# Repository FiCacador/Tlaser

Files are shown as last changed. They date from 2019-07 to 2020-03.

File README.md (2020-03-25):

# Tlaser

Tlaser is a laser engraver designed as proof of concept of a new motion system, coreXY cantilever. It's called Tlaser because this motion system, and thus this machine, is shaped like a T.  
  
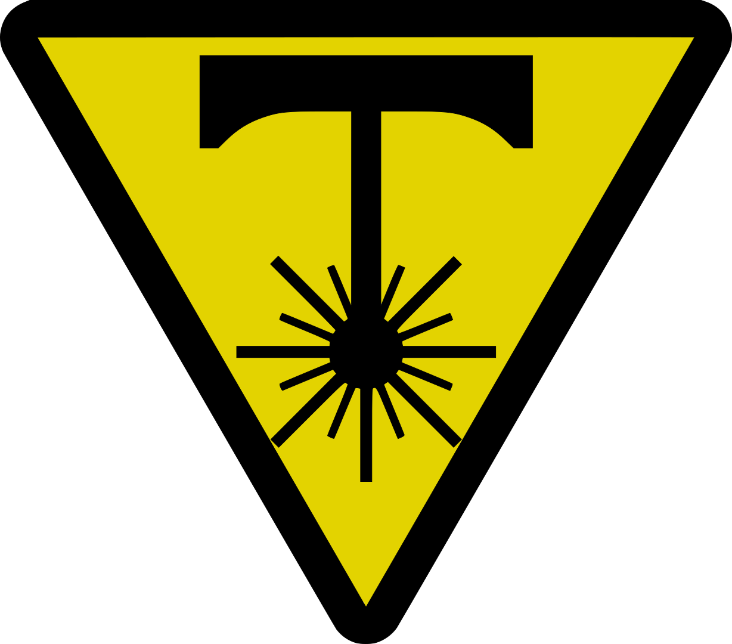
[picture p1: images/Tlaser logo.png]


### Main features:

- **CoreXY cantilever**
- **5500mW blue laser**
- **315mm x 205mm engraving area**
- **Linear guide rails**
- **Adjustable height at each corner**
- **3D printed**  
  
## [Video of Tlaser in action!](https://youtu.be/NjZCqPt6v3c)

<p float="center">
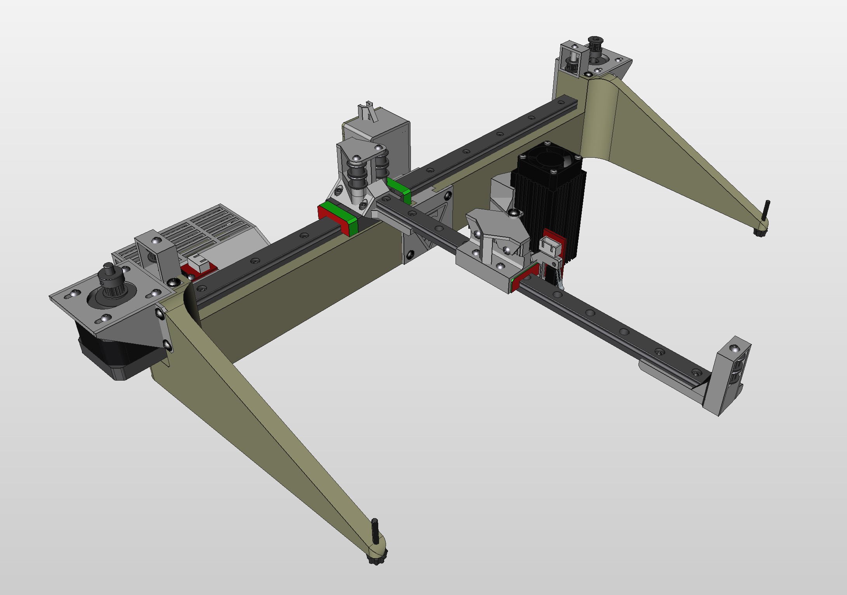
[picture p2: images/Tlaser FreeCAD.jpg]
  
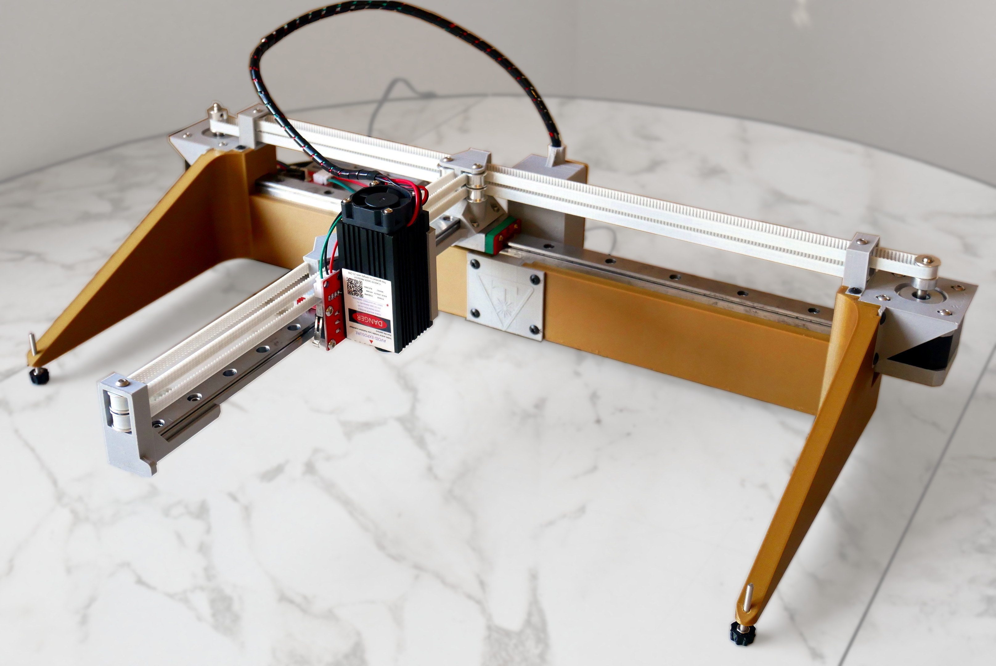
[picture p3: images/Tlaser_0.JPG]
  
</p>

## CoreXY cantilever

Tlaser was developed to validate and demonstrate a new motion system, which the author named  *CoreXY cantilever*.  
CoreXY cantilever has the same kinematics as [CoreXY](https://corexy.com/theory.html), so it is easy to configure in existing firmware like Grbl or Marlin. If the motors rotate to the same directions, the head travels along the X axis. If the motors rotate to opposite directions, the head travels along the Y axis.  
This mechanism has two belts, one over another, each on a circuit shaped like a T. Both circuits have pulleys at the middle on both sides and at the end of the cantilever.  
The upper belt is driven by the motor at the right end, has a pulley on the left end and is locked to the left side of the carrier. The lower is symmetric, motor on the left, pulley on the right, locked to the right side of the carrier.

<p float="center">
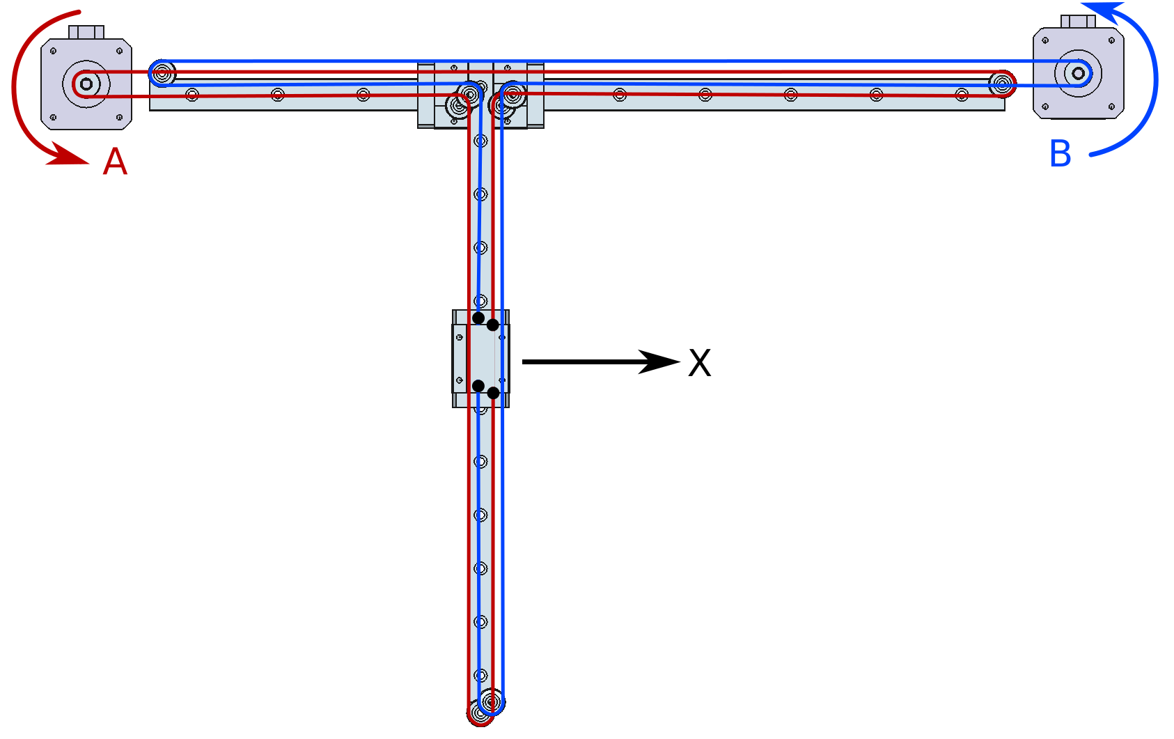
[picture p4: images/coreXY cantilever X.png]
  
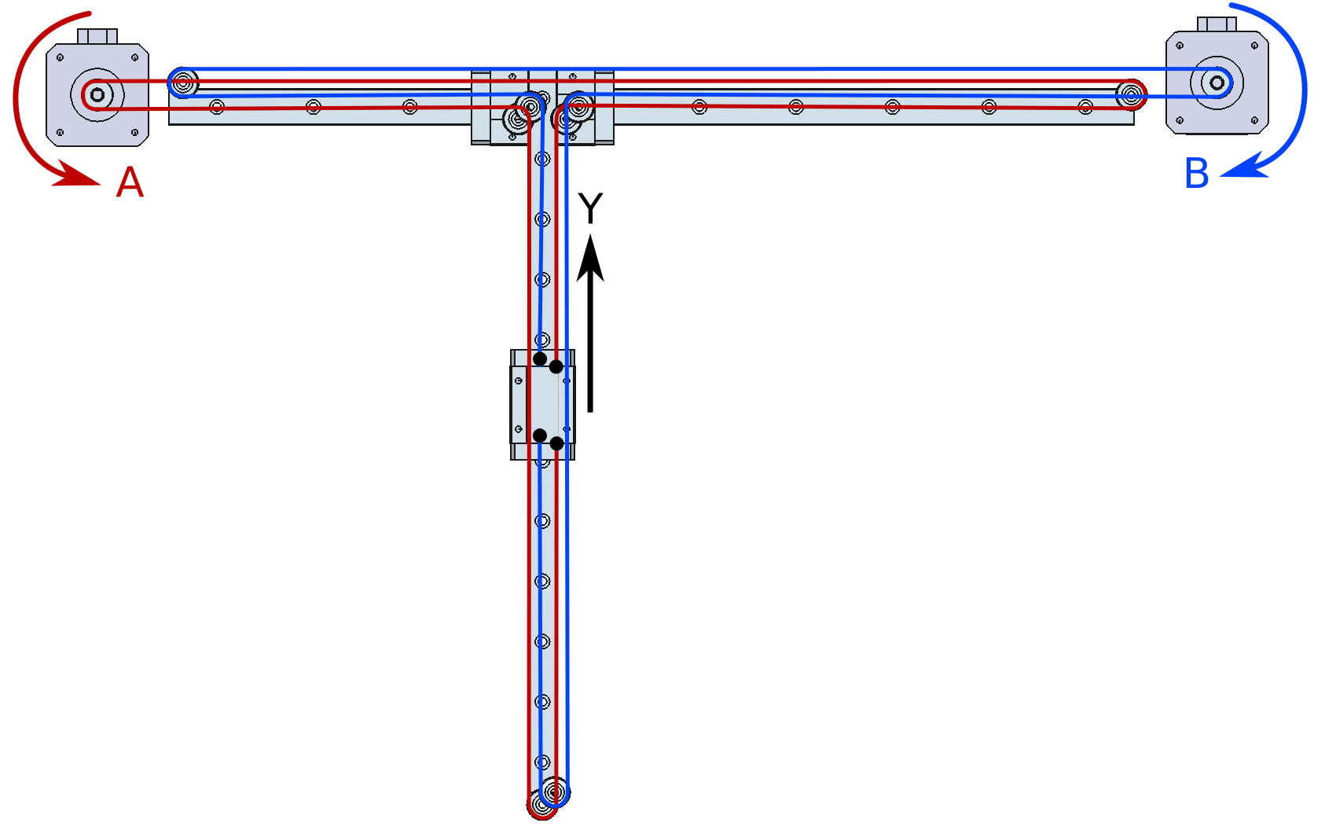
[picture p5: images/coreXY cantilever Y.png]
  
</p>

## Hardware

The following parts are required for building this machine:

- [5.5W 445NM blue laser module w/ power supply](http://s.click.aliexpress.com/e/bAbwR1Wg)
- [MGN12H 300mm and MGN15H 400mm Blocks and Rails](http://s.click.aliexpress.com/e/bKj8dYfI)
- [2 Nema 17 stepper motors](http://s.click.aliexpress.com/e/cpg92iXI)
- [Arduino Uno R3 /w CNC shield v3 and A4988 stepper drivers](http://s.click.aliexpress.com/e/b7E6Xk5a)
- [2 mechanical endstops](http://s.click.aliexpress.com/e/CIG3mQk)
- [Timing belt GT2 6mm 5m](http://s.click.aliexpress.com/e/belvtmGu)
- [2 Belt drive Pulleys GT2 16 teeth bore 5mm](https://s.click.aliexpress.com/e/_d7v8uTQ)
- [GT2 pulleys, 4 w/ 16 teeth and 4 w/ no teeth](https://s.click.aliexpress.com/e/_dZuRE9S)
- [M3x6 and M3x30 round head hex bolts](http://s.click.aliexpress.com/e/cScWFTX6)
- [M3x8 socket head hex bolts](http://s.click.aliexpress.com/e/b72TH5Nm)
- [M3x12 self tapping bolts](http://s.click.aliexpress.com/e/bZMmlnQu)
- [M3x50 socket head bolts](http://s.click.aliexpress.com/e/t3QLC2k)
- [M3 hex nuts](http://s.click.aliexpress.com/e/nRG0NIC)

The list above contains affiliate links.  
The total cost should be below €150 / $165 USD, 3D printed parts not included.
For a more detailed table with quantities check the [Bill of Materials](https://github.com/FiCacador/Tlaser/raw/master/BOM.ods).

## 3D Printed parts

All parts are already correctly oriented for ease of printing and available in [STL files](https://github.com/FiCacador/Tlaser/tree/master/STLs) and [AMF files](https://github.com/FiCacador/Tlaser/tree/master/AMFs).  
Dimensional accuracy is very important. This is an assembly of mechanical parts designed to fit tight, the slightest overextrusion will make for a hard time during the assembly.  
Due to proximity to the stepper motors and laser module, [Laser Mount](https://github.com/FiCacador/Tlaser/blob/master/STLs/Laser%20Mount.stl), [Motor Mount Left](https://github.com/FiCacador/Tlaser/blob/master/STLs/Motor%20Mount%20Left.stl) and [Motor Mount Right](https://github.com/FiCacador/Tlaser/blob/master/STLs/Motor%20Mount%20Right.stl) should be printed with a more heat resistant material, like ABS or PETG.  
Recommended settings: 0.5 mm line width, 0.2 mm layer height, 2 mm wall thickness, over 15% infill. Some parts require support. [Base Left](https://github.com/FiCacador/Tlaser/blob/master/STLs/Base%20Left.stl) and [Base Right](https://github.com/FiCacador/Tlaser/blob/master/STLs/Base%20Right.stl) are prone to warping, requiring good bed adhesion.  
Total printing time around 38h. Total filament used approximately 600g.

## Assembly

### [Video of Tlaser Exploded Assembly on FreeCAD](https://youtu.be/6Z7JV-q1IXA)

An [Exploded Assembly CAD file](https://github.com/FiCacador/Tlaser/raw/master/CAD/Tlaser%20Exploded%20Assembly.FCStd) for [FreeCAD](https://www.freecadweb.org/) with the [Exploded Assembly workbench](https://github.com/JMG1/ExplodedAssembly) added is available to guide the assembly process.  
Required tools are a set of hex key wrenches, a philips screwdriver, a small flat head screwdriver, a rubber mallet and a wire cutter.  
The controller wiring is pretty straight forward, the exceptions being the laser TTL connects to the Z+ endstop pins and the red wire is left out when connecting the X and Y endstops. The power supply and 12V laser PCB cables need to be cut so both can be connected to the same respective + and - on the CNC shield.

<p float="center">
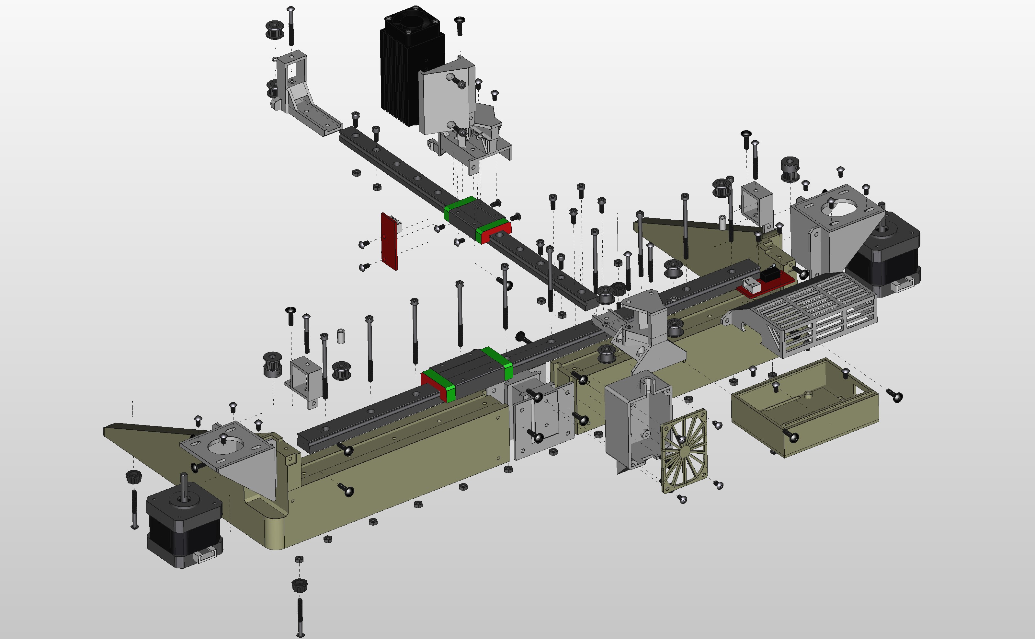
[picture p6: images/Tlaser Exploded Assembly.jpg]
  
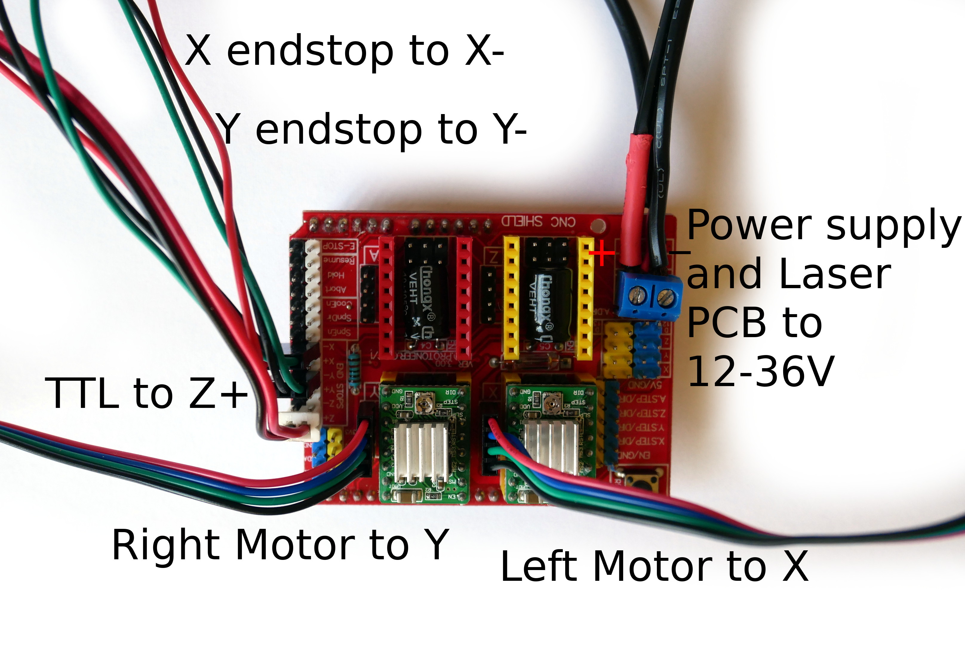
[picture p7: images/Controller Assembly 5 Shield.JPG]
  
</p>

## Firmware

An Arduino running [Grbl](https://github.com/gnea/grbl) is used to control Tlaser. It uses Grbl version 1.1g with a modified [config.h file](https://github.com/FiCacador/Tlaser/blob/master/Firmware/grbl-v1.1/grbl/config.h) with the configuration and default values that better suit this machine.  
You can find an hex file and the source code of Grbl for Tlaser [here](https://github.com/FiCacador/Tlaser/tree/master/Firmware).  
Instructions on how to [flash Grbl to an Arduino](https://github.com/gnea/grbl/wiki/Flashing-Grbl-to-an-Arduino) or alternatively [compile and upload Grbl](https://github.com/gnea/grbl/wiki/Compiling-Grbl) can be found on the [Grbl Wiki](https://github.com/gnea/grbl/wiki).  
Grbl is distributed under the GPLv3 license and is developed by Sungeun K. Jeon Ph.D.

## CAM Software

[LaserWeb4](https://github.com/LaserWeb/LaserWeb4/wiki) is simple yet powerful, graphically pleasing open source laser CAM software available for Windows, Mac and Linux.  
A [file containing Tlaser profile](https://github.com/FiCacador/Tlaser/blob/master/CAM%20profiles/laserweb-profiles-tlaser.json) for LaserWeb4 v4.0.996 is available.  
There are many valid laser CAM software options, use whatever one you like the most.

## Design

This project was designed using [FreeCAD](https://www.freecadweb.org/). There are more powerful and certainly more user friendly options, but none is actually free (of charge, of licensing, of login) and available for Windows, Mac and Linux.  
Designed with FreeCAD version 0.18.3 with the added workbenches [Fasteners](https://github.com/shaise/FreeCAD_FastenersWB), [A2plus](https://github.com/kbwbe/A2plus) and [Exploded Assembly](https://github.com/JMG1/ExplodedAssembly).  
You can find the CAD files for the individual parts and the assembly [here](https://github.com/FiCacador/Tlaser/tree/master/CAD).  
All the features and sketches of the 3D Printed parts are named, for ease of understanding and editing

---

Tlaser is developed by Filipe Caçador.

## License

Tlaser is published under the Creative Commons [Attribution-ShareAlike 4.0 International (CC BY-SA 4.0)](https://creativecommons.org/licenses/by-sa/4.0/) Public License.  
Under this license, anyone can share, copy, redistribute, edit, remix and develop this work, for any purpose, as long as credit is attributed to the original author and any further developments are distributed under the same license.  
No warranty of any kind is provided and the author is not liable for any losses, damages or injuries in any way related to this work.

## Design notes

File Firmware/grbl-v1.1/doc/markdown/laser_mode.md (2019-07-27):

## Grbl v1.1 Laser Mode

**_DISCLAIMER: Lasers are extremely dangerous devices. They can instantly cause fires and permanently damage your vision. Please read and understand all related documentation for your laser prior to using it. The Grbl project is not resposible for any damage or issues the firmware may cause, as defined by its GPL license._**

----

Outlined in this document is how Grbl alters its running conditions for the new laser mode to provide both improved performance and attempting to enforce some basic user safety precautions.

## Laser Mode Overview

The main difference between default Grbl operation and the laser mode is how the spindle/laser output is controlled with motions involved. Every time a spindle state `M3 M4 M5` or spindle speed `Sxxx` is altered, Grbl would come to a stop, allow the spindle to change, and then continue. This is the normal operating procedure for a milling machine spindle. It needs time to change speeds. 

However, if a laser starts and stops like this for every spindle change, this leads to scorching and uneven cutting/engraving! Grbl's new laser mode prevents unnecessary stops whenever possible and adds a new dynamic laser power mode that automagically scales power based on current speed related to programmed rate. So, you can get super clean and crisp results, even on a low-acceleration machine!

Enabling or disabling Grbl's laser mode is easy. Just alter the **$32** Grbl setting. 
- **To Enable**: Send Grbl a `$32=1` command. 
- **To Disable:** Send Grbl a `$32=0` command.

**WARNING:** If you switch back from laser mode to a spindle for milling, you **MUST** disable laser mode by sending Grbl a `$32=0` command. Milling operations require the spindle to get up to the right rpm to cut correctly and to be **safe**, helping to prevent a tool from breaking and flinging metal shards everywhere. With laser mode disabled, Grbl will briefly pause upon any spindle speed or state change to give the spindle a chance to get up to speed before continuing.

## Laser Mode Operation

When laser mode is enabled, Grbl controls laser power by varying the **0-5V** voltage from the spindle PWM D11 pin. **0V** should be treated as disabled, while **5V** is full power. Intermediate output voltages are also assumed to be linear with laser power, such that **2.5V** is approximate 50% laser power. (A compile time option exists to shift this linear model to start at a non-zero voltage.) 

By default, the spindle PWM frequency is **1kHz**, which is the recommended PWM frequency for most current Grbl-compatible lasers system. If a different frequency is required, this may be altered by editing the `cpu_map.h` file. 

The laser is enabled with the `M3` spindle CW and `M4` spindle CCW commands. These enable two different laser modes that are advantageous for different reasons each.
	
- **`M3` Constant Laser Power Mode:**

    - Constant laser power mode simply keeps the laser power as programmed, regardless if the machine is moving, accelerating, or stopped. This provides better control of the laser state. With a good G-code program, this can lead to more consistent cuts in more difficult materials. 
    
    - For a clean cut and prevent scorching with `M3` constant power mode, it's a good idea to add lead-in and lead-out motions around the line you want to cut to give some space for the machine to accelerate and decelerate.

    - NOTE: `M3` can be used to keep the laser on for focusing.

- **`M4` Dynamic Laser Power Mode:**
    - Dynamic laser power mode will automatically adjust laser power based on the current speed relative to the programmed rate. It essentially ensures the amount of laser energy along a cut is consistent even though the machine may be stopped or actively accelerating. This is very useful for clean, precise engraving and cutting on simple materials across a large range of G-code generation methods by CAM programs. It will generally run faster and may be all you need to use.
    
    - Grbl calculates laser power based on the assumption that laser power is linear with speed and the material. Often, this is not the case. Lasers can cut differently at varying power levels and some materials may not cut well at a particular speed and/power. In short, this means that dynamic power mode may not work for all situations. Always do a test piece prior to using this with a new material or machine.
		
    - When not in motion, `M4` dynamic mode turns off the laser. It only turns on when the machine moves. This generally makes the laser safer to operate, because, unlike `M3`, it will never burn a hole through your table, if you stop and forget to turn `M3` off in time.

Describe below are the operational changes to Grbl when laser mode is enabled. Please read these carefully and understand them fully, because nothing is worse than a garage _**fire**_.

- Grbl will move continuously through **consecutive** motion commands when programmed with a new `S` spindle speed (laser power). The spindle PWM pin will be updated instantaneously through each motion without stopping.
	- Example: The following set of g-code commands will not pause between each of them when laser mode is enabled, but will pause when disabled.
	
		```
		G1 X10 S100 F50
		G1 X0 S90
		G2 X0 I5 S80
		``` 
	- Grbl will enforce a laser mode motion stop in a few circumstances. Primarily to ensure alterations stay in sync with the g-code program.

		- Any `M3`, `M4`, `M5` spindle state _change_. 
		- `M3` only and no motion programmed: A `S` spindle speed _change_.
		- `M3` only and no motion programmed: A `G1 G2 G3` laser powered state _change_ to `G0 G80` laser disabled state.
		- NOTE: `M4` does not stop for anything but a spindle state _change_.

- The laser will only turn on when Grbl is in a `G1`, `G2`, or `G3` motion mode. 

	- In other words, a `G0` rapid motion mode or `G38.x` probe cycle will never turn on and always disable the laser, but will still update the running modal state. When changed to a `G1 G2 G3` modal state, Grbl will immediately enable the laser based on the current running state.
	
	- Please remember that `G0` is the default motion mode upon power up and reset. You will need to alter it to `G1`, `G2`, or `G3` if you want to manually turn on your laser. This is strictly a safety measure.
	
	- Example: `G0 M3 S1000` will not turn on the laser, but will set the laser modal state to `M3` enabled and power of `S1000`. A following `G1` command will then immediately be set to `M3` and `S1000`.

	- To have the laser powered during a jog motion, first enable a valid motion mode and spindle state. The following jog motions will inherit and maintain the previous laser state. Please use with caution though. This ability is primarily to allow turning on the laser on a _very low_ power to use the laser dot to jog and visibly locate the start position of a job.

- An `S0` spindle speed of zero will turn off the laser. When programmed with a valid laser motion, Grbl will disable the laser instantaneously without stopping for the duration of that motion and future motions until set greater than zero..

	- `M3` constant laser mode, this is a great way to turn off the laser power while continuously moving between a `G1` laser motion and a `G0` rapid motion without having to stop. Program a short `G1 S0` motion right before the `G0` motion and a `G1 Sxxx` motion is commanded right after to go back to cutting.

-----
###CAM Developer Implementation Notes

TODO: Add some suggestions on how to write laser G-code for Grbl. 

- When using `M3` constant laser power mode, try to avoid force-sync conditions during a job whenever possible. Basically every spindle speed change must be accompanied by a valid motion. Any motion is fine, since Grbl will automatically enable and disable the laser based on the modal state. Avoid a `G0` and `G1` command with no axis words in this mode and in the middle of a job.

- Ensure smooth motions throughout by turning the laser on and off without an `M3 M4 M5` spindle state command. There are two ways to do this:

    - _Program a zero spindle speed `S0`_: `S0` is valid G-code and turns off the spindle/laser without changing the spindle state. In laser mode, Grbl will smoothly move through consecutive motions and turn off the spindle. Conversely, you can turn on the laser with a spindle speed `S` greater than zero. Remember that `M3` constant power mode requires any spindle speed `S` change to be programmed with a motion to allow continuous motion, while `M4` dynamic power mode does not.

    - _Program an unpowered motion between powered motions_: If you are traversing between parts of a raster job that don't need to have the laser powered, program a `G0` rapid between them. `G0` enforces the laser to be disabled automatically. The last spindle speed programmed doesn't change, so if a valid powered motion, like a `G1` is executed after, it'll immediately re-power the laser with the last programmed spindle speed when executing that motion.

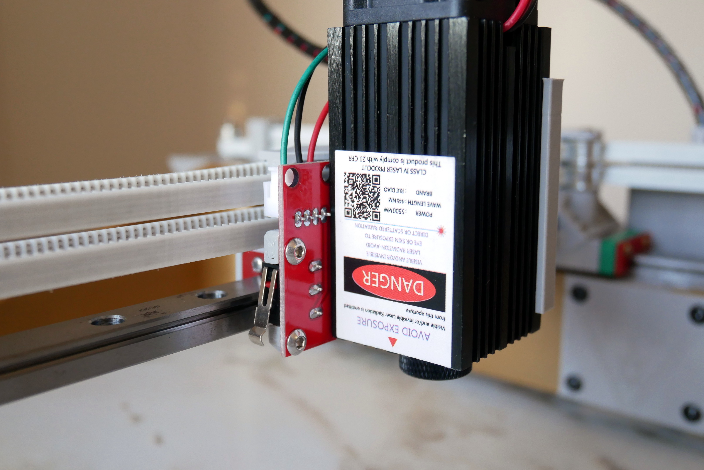
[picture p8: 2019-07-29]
images/Tlaser_8.JPG

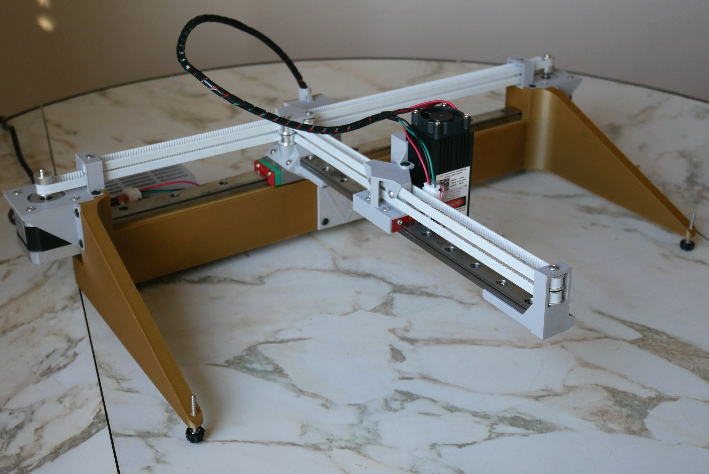
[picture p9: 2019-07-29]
images/Tlaser_1.JPG

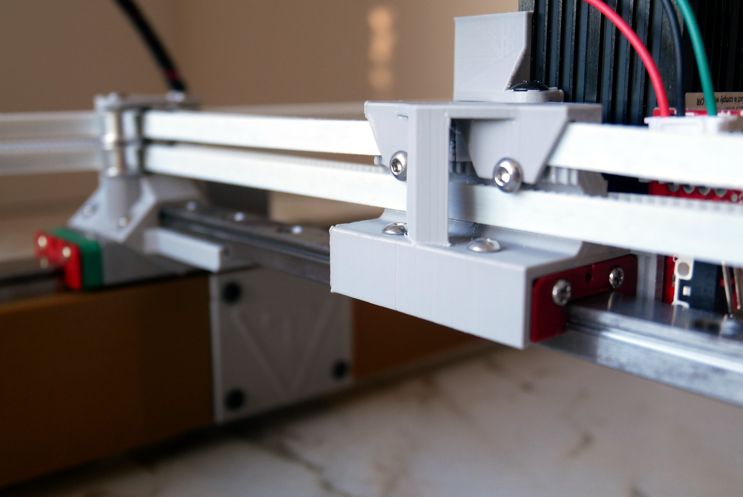
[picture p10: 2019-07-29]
images/Tlaser_5.JPG

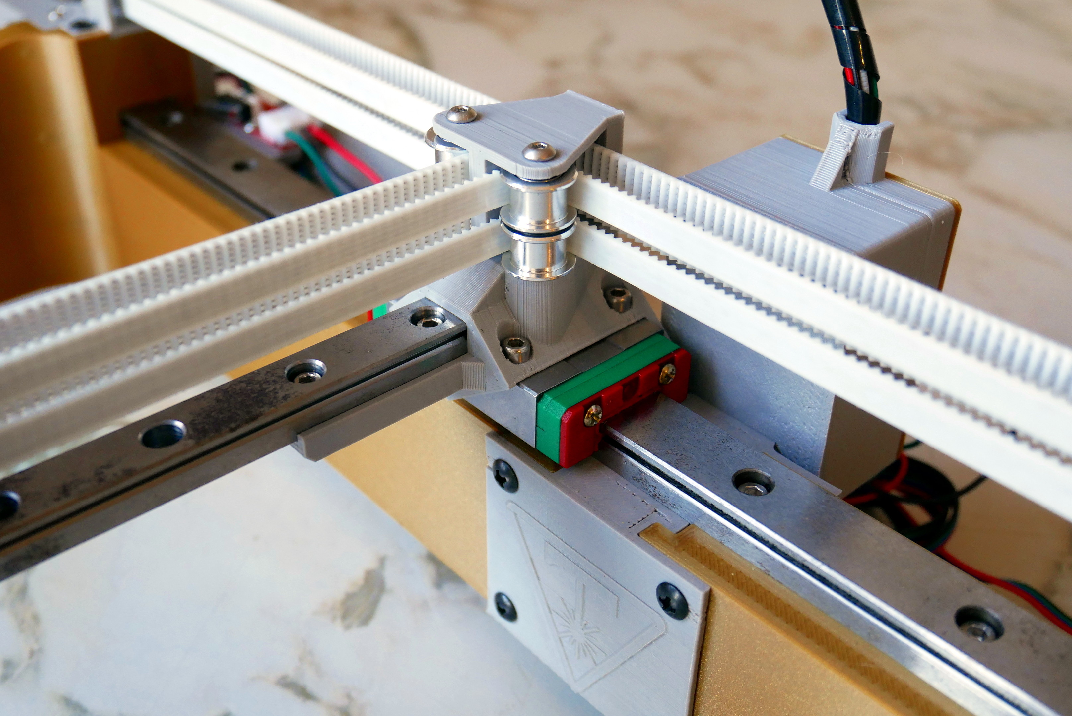
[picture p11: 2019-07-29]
images/Tlaser_6.JPG

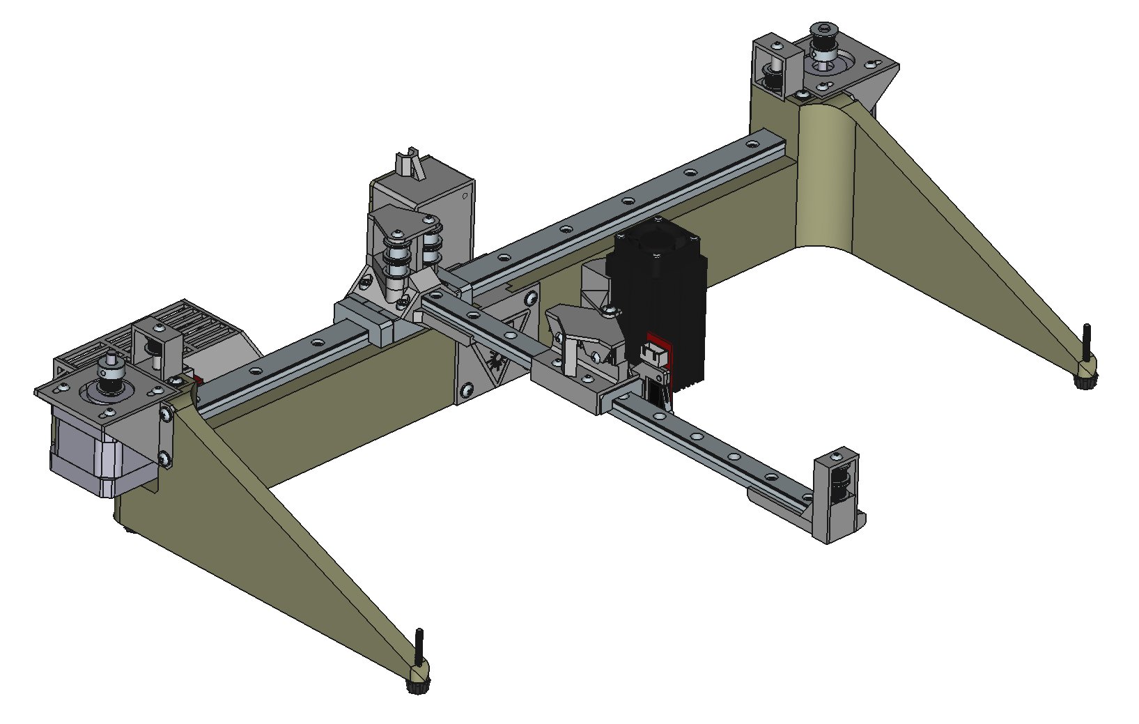
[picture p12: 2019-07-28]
images/Tlaser_FreeCAD.png

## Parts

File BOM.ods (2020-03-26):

Bill of Materials – Tlaser
3D Printed
Quantity | Description | STL file | CAD file | AMF file
1 | Base Left | stl (https://github.com/FiCacador/Tlaser/blob/master/STLs/Base%20Left.stl) | fcstd (https://github.com/FiCacador/Tlaser/raw/master/CAD/3D%20Printed/Base%20Left.FCStd) | amf (https://github.com/FiCacador/Tlaser/raw/master/AMFs/Base%20Left.amf)
1 | Base Middle | stl (https://github.com/FiCacador/Tlaser/blob/master/STLs/Base%20Middle.stl) | fcstd (https://github.com/FiCacador/Tlaser/raw/master/CAD/3D%20Printed/Base%20Middle.FCStd) | amf (https://github.com/FiCacador/Tlaser/raw/master/AMFs/Base%20Middle.amf)
1 | Base Right | stl (https://github.com/FiCacador/Tlaser/blob/master/STLs/Base%20Right.stl) | fcstd (https://github.com/FiCacador/Tlaser/raw/master/CAD/3D%20Printed/Base%20Right.FCStd) | amf (https://github.com/FiCacador/Tlaser/raw/master/AMFs/Base%20Right.amf)
4 | Bottom Stand | stl (https://github.com/FiCacador/Tlaser/blob/master/STLs/Bottom%20Stand.stl) | fcstd (https://github.com/FiCacador/Tlaser/raw/master/CAD/3D%20Printed/Bottom%20Stand.FCStd) | amf (https://github.com/FiCacador/Tlaser/raw/master/AMFs/Bottom%20Stand.amf)
1 | Controller Case Bottom | stl (https://github.com/FiCacador/Tlaser/blob/master/STLs/Controller%20Case%20Bottom.stl) | fcstd (https://github.com/FiCacador/Tlaser/raw/master/CAD/3D%20Printed/Controller%20Case%20Bottom.FCStd) | amf (https://github.com/FiCacador/Tlaser/raw/master/AMFs/Controller%20Case%20Bottom.amf)
1 | Controller Case Top | stl (https://github.com/FiCacador/Tlaser/blob/master/STLs/Controller%20Case%20Top.stl) | fcstd (https://github.com/FiCacador/Tlaser/raw/master/CAD/3D%20Printed/Controller%20Case%20Top.FCStd) | amf (https://github.com/FiCacador/Tlaser/raw/master/AMFs/Controller%20Case%20Top.amf)
1 | Endstop Mount | stl (https://github.com/FiCacador/Tlaser/blob/master/STLs/Laser%20Mount.stl) | fcstd (https://github.com/FiCacador/Tlaser/raw/master/CAD/3D%20Printed/Endstop%20Mount.FCStd) | amf (https://github.com/FiCacador/Tlaser/raw/master/AMFs/Laser%20Mount.amf)
1 | Laser Mount | stl (https://github.com/FiCacador/Tlaser/blob/master/STLs/Laser%20Mount.stl) | fcstd (https://github.com/FiCacador/Tlaser/raw/master/CAD/3D%20Printed/Laser%20Mount.FCStd) | amf (https://github.com/FiCacador/Tlaser/raw/master/AMFs/Laser%20Mount.amf)
1 | Laser PCB Box | stl (https://github.com/FiCacador/Tlaser/blob/master/STLs/Laser%20PCB%20Box.stl) | fcstd (https://github.com/FiCacador/Tlaser/raw/master/CAD/3D%20Printed/Laser%20PCB%20Box.FCStd) | amf (https://github.com/FiCacador/Tlaser/raw/master/AMFs/Laser%20PCB%20Box.amf)
1 | Laser PCB Box Lid | stl (https://github.com/FiCacador/Tlaser/blob/master/STLs/Laser%20PCB%20Box%20Lid.stl) | fcstd (https://github.com/FiCacador/Tlaser/raw/master/CAD/3D%20Printed/Laser%20PCB%20Box%20Lid.FCStd) | amf (https://github.com/FiCacador/Tlaser/raw/master/AMFs/Laser%20PCB%20Box%20Lid.amf)
1 | Motor Mount Left | stl (https://github.com/FiCacador/Tlaser/blob/master/STLs/Motor%20Mount%20Left.stl) | fcstd (https://github.com/FiCacador/Tlaser/raw/master/CAD/3D%20Printed/Motor%20Mount%20Left.FCStd) | amf (https://github.com/FiCacador/Tlaser/raw/master/AMFs/Motor%20Mount%20Left.amf)
1 | Motor Mount Right | stl (https://github.com/FiCacador/Tlaser/blob/master/STLs/Motor%20Mount%20Right.stl) | fcstd (https://github.com/FiCacador/Tlaser/raw/master/CAD/3D%20Printed/Motor%20Mount%20Right.FCStd) | amf (https://github.com/FiCacador/Tlaser/raw/master/AMFs/Motor%20Mount%20Right.amf)
1 | Pulley Cage Left | stl (https://github.com/FiCacador/Tlaser/blob/master/STLs/Pulley%20Cage%20Left.stl) | fcstd (https://github.com/FiCacador/Tlaser/raw/master/CAD/3D%20Printed/Pulley%20Cage%20Left.FCStd) | amf (https://github.com/FiCacador/Tlaser/raw/master/AMFs/Pulley%20Cage%20Left.amf)
1 | Pulley Cage Right | stl (https://github.com/FiCacador/Tlaser/blob/master/STLs/Motor%20Mount%20Right.stl) | fcstd (https://github.com/FiCacador/Tlaser/raw/master/CAD/3D%20Printed/Pulley%20Cage%20Right.FCStd) | amf (https://github.com/FiCacador/Tlaser/raw/master/AMFs/Motor%20Mount%20Right.amf)
1 | Rail Base | stl (https://github.com/FiCacador/Tlaser/blob/master/STLs/Rail%20Base.stl) | fcstd (https://github.com/FiCacador/Tlaser/raw/master/CAD/3D%20Printed/Rail%20Base.FCStd) | amf (https://github.com/FiCacador/Tlaser/raw/master/AMFs/Rail%20Base.amf)
1 | Rail Carrier | stl (https://github.com/FiCacador/Tlaser/blob/master/STLs/Rail%20Carrier.stl) | fcstd (https://github.com/FiCacador/Tlaser/raw/master/CAD/3D%20Printed/Rail%20Carrier.FCStd) | amf (https://github.com/FiCacador/Tlaser/raw/master/AMFs/Rail%20Carrier.amf)
1 | Rail Tip | stl (https://github.com/FiCacador/Tlaser/blob/master/STLs/Rail%20Tip.stl) | fcstd (https://github.com/FiCacador/Tlaser/raw/master/CAD/3D%20Printed/Rail%20Tip.FCStd) | amf (https://github.com/FiCacador/Tlaser/raw/master/AMFs/Rail%20Tip.amf)
3 | Spacer | stl (https://github.com/FiCacador/Tlaser/blob/master/STLs/Spacer.stl) | fcstd (https://github.com/FiCacador/Tlaser/raw/master/CAD/3D%20Printed/Spacer.FCStd) | amf (https://github.com/FiCacador/Tlaser/raw/master/AMFs/Spacer.amf)
2 | Tall Spacer | stl (https://github.com/FiCacador/Tlaser/blob/master/STLs/Tall%20Spacer.stl) | fcstd (https://github.com/FiCacador/Tlaser/raw/master/CAD/3D%20Printed/Tall%20Spacer.FCStd) | amf (https://github.com/FiCacador/Tlaser/raw/master/AMFs/Tall%20Spacer.amf)
Mechanical
Quantity | Description | Affiliate link | CAD file
1 | Rail MGN12 300mm | AliExpress (http://s.click.aliexpress.com/e/bKj8dYfI) | fcstd (https://github.com/FiCacador/Tlaser/raw/master/CAD/Mechanical/Rail%20MGN12%20300mm.fcstd)
1 | Block MGN12H | AliExpress (http://s.click.aliexpress.com/e/bKj8dYfI) | fcstd (https://github.com/FiCacador/Tlaser/raw/master/CAD/Mechanical/Block%20MGN12H.fcstd)
1 | Rail MGN15 400mm | AliExpress (http://s.click.aliexpress.com/e/bKj8dYfI) | fcstd (https://github.com/FiCacador/Tlaser/raw/master/CAD/Mechanical/Rail%20MGN15%20400mm.fcstd)
1 | Block MGN15H | AliExpress (http://s.click.aliexpress.com/e/bKj8dYfI) | fcstd (https://github.com/FiCacador/Tlaser/raw/master/CAD/Mechanical/Block%20MGN15H.fcstd)
1 | Timing Belt GT2 6mm 5m | AliExpress (http://s.click.aliexpress.com/e/belvtmGu)
2 | Belt Drive Pulley GT2 16 teeth 5mm | AliExpress (https://s.click.aliexpress.com/e/_d7v8uTQ) | fcstd (https://github.com/FiCacador/Tlaser/raw/master/CAD/Mechanical/Driver%20Pulley.fcstd)
4 | Pulley GT2 6mm 16T no teeth Bore 3mm | AliExpress (https://s.click.aliexpress.com/e/_dZuRE9S) | fcstd (https://github.com/FiCacador/Tlaser/raw/master/CAD/Mechanical/Pulley.fcstd)
4 | Pulley GT2 6mm 16T with teeth Bore 3mm | AliExpress (https://s.click.aliexpress.com/e/_dZuRE9S) | fcstd (https://github.com/FiCacador/Tlaser/raw/master/CAD/Mechanical/Pulley%2016T.FCStd)
Fasteners
Quantity | Description | Affiliate link | CAD file
28 | Bolt M3x6 Round Head Hex | AliExpress (http://s.click.aliexpress.com/e/cScWFTX6) | fcstd (https://github.com/FiCacador/Tlaser/raw/master/CAD/Fasteners/M3x6.FCStd)
10 | Bolt M3x8 Socket Head Hex | AliExpress (http://s.click.aliexpress.com/e/b72TH5Nm) | fcstd (https://github.com/FiCacador/Tlaser/raw/master/CAD/Fasteners/M3x8.FCStd)
26 | Bolt M3x12 Self Tapping | AliExpress (http://s.click.aliexpress.com/e/bZMmlnQu) | fcstd (https://github.com/FiCacador/Tlaser/raw/master/CAD/Fasteners/M3x12%20tapping.FCStd)
9 | Bolt M3x30 Round Head Hex | AliExpress (http://s.click.aliexpress.com/e/cScWFTX6) | fcstd (https://github.com/FiCacador/Tlaser/raw/master/CAD/Fasteners/M3x30.FCStd)
10 | Bolt M3x50 Socket Head Hex | AliExpress (http://s.click.aliexpress.com/e/t3QLC2k) | fcstd (https://github.com/FiCacador/Tlaser/raw/master/CAD/Fasteners/M3x50.FCStd)
18 | Nut M3 Hex | AliExpress (http://s.click.aliexpress.com/e/nRG0NIC) | fcstd (https://github.com/FiCacador/Tlaser/raw/master/CAD/Fasteners/M3%20Nut.FCStd)
Electronics
Quantity | Description | Affiliate link | CAD file
1 | Arduino Uno R3 | AliExpress (http://s.click.aliexpress.com/e/b7E6Xk5a)
1 | CNC Shield v3 | AliExpress (http://s.click.aliexpress.com/e/b7E6Xk5a)
2 | Stepper Driver A4988 | AliExpress (http://s.click.aliexpress.com/e/b7E6Xk5a)
1 | Laser Module 5.5w 445NM blue laser | AliExpress (http://s.click.aliexpress.com/e/bAbwR1Wg) | fcstd (https://github.com/FiCacador/Tlaser/raw/master/CAD/Electronics/Laser%20Module%205500mW.FCStd)
1 | Power Supply 12V 5A | AliExpress (http://s.click.aliexpress.com/e/bAbwR1Wg)
2 | Mechanical Endstop for RAMPS | AliExpress (http://s.click.aliexpress.com/e/CIG3mQk) | fcstd (https://github.com/FiCacador/Tlaser/raw/master/CAD/Electronics/Endstop.FCStd)
2 | Stepper Motor Nema 17 42BYGH | AliExpress (http://s.click.aliexpress.com/e/cpg92iXI) | fcstd (https://github.com/FiCacador/Tlaser/raw/master/CAD/Electronics/Stepper%20motor%20Nema%2017%2042BYGH%2038mm.fcstd)

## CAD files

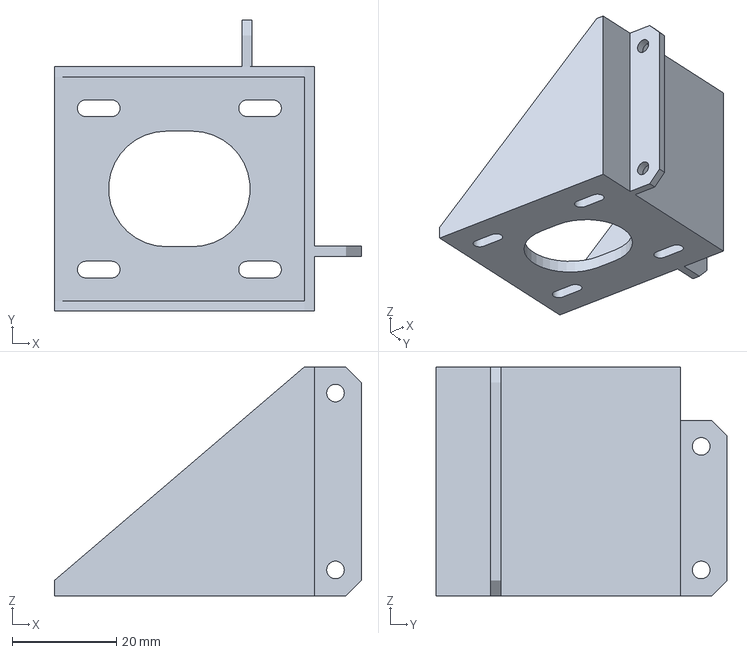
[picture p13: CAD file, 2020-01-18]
AMFs/Motor Mount Left.amf
59.0 x 56.0 x 44.0 mm

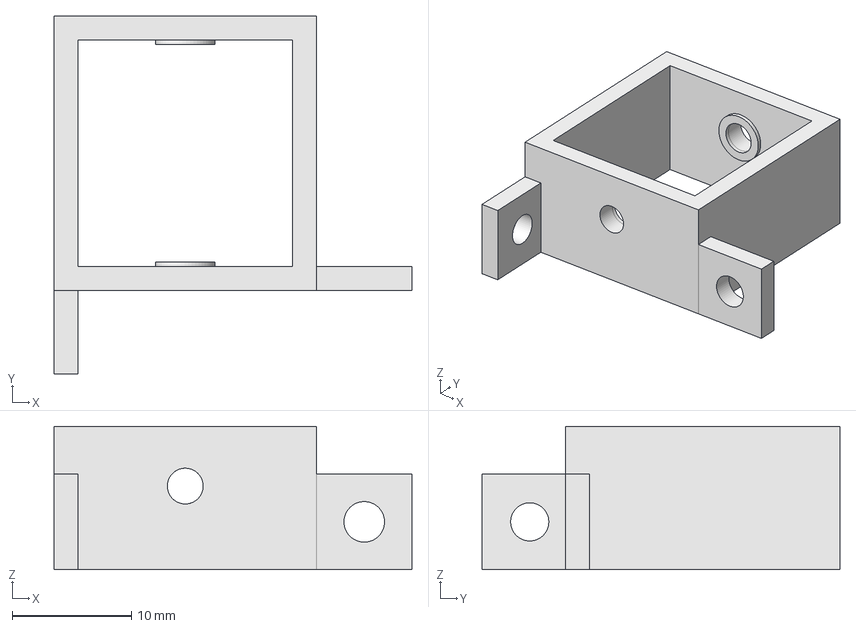
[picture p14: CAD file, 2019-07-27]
CAD/3D Printed/Pulley Cage Right.FCStd
30.0 x 30.0 x 12.0 mm

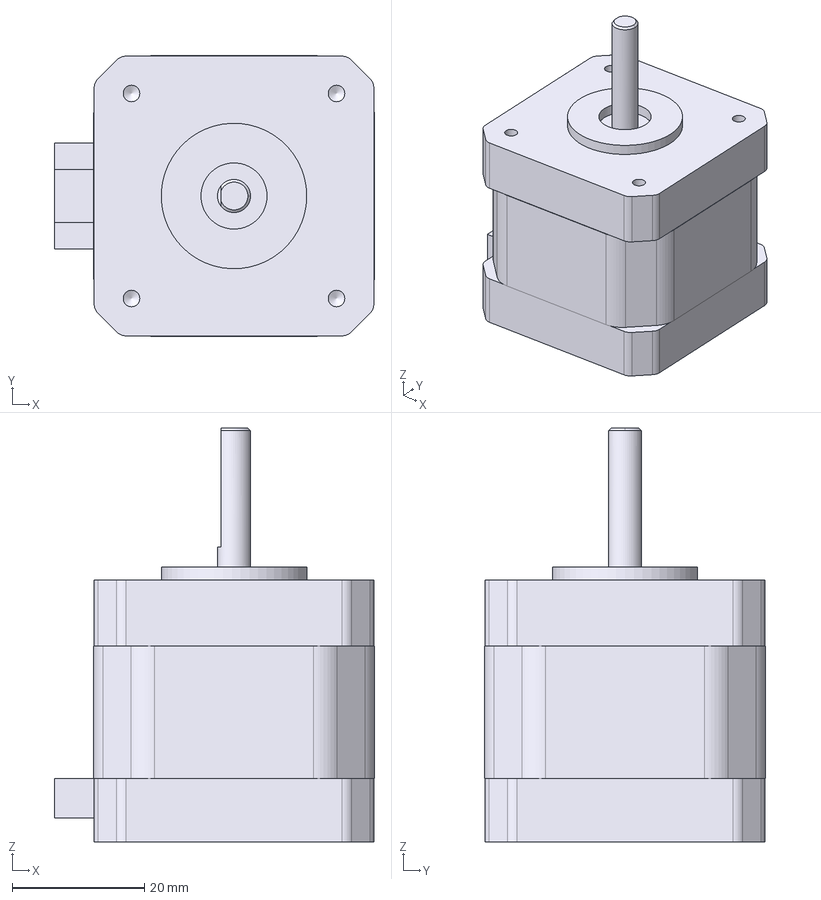
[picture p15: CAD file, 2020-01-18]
CAD/Electronics/Stepper motor Nema 17 42BYGH 38mm.fcstd
48.4 x 42.5 x 62.6 mm

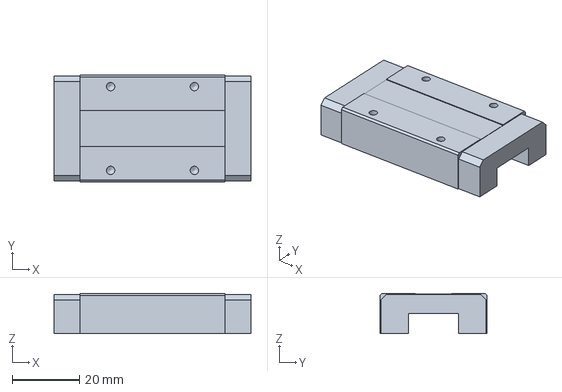
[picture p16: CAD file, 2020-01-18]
CAD/Mechanical/Block MGN15H.fcstd
58.8 x 32.0 x 12.0 mm

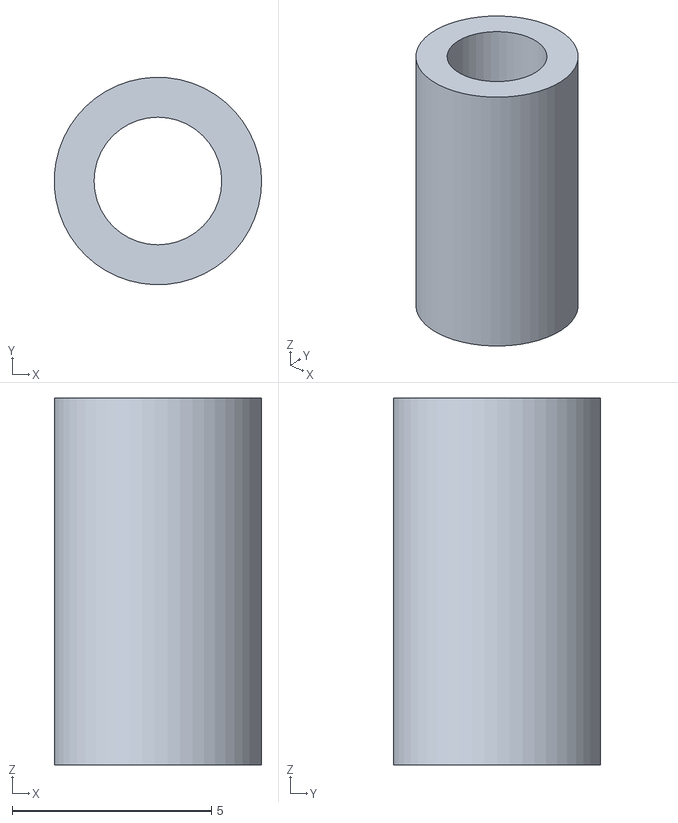
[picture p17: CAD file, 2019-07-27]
STLs/Tall Spacer.stl
5.20 x 5.20 x 9.20

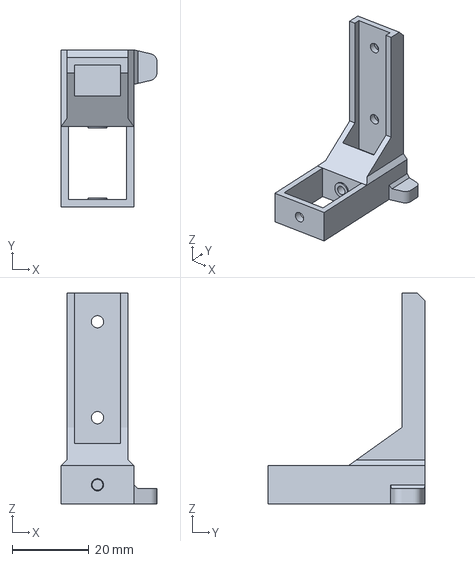
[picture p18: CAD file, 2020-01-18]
AMFs/Rail Tip.amf
25.0 x 41.0 x 55.0 mm

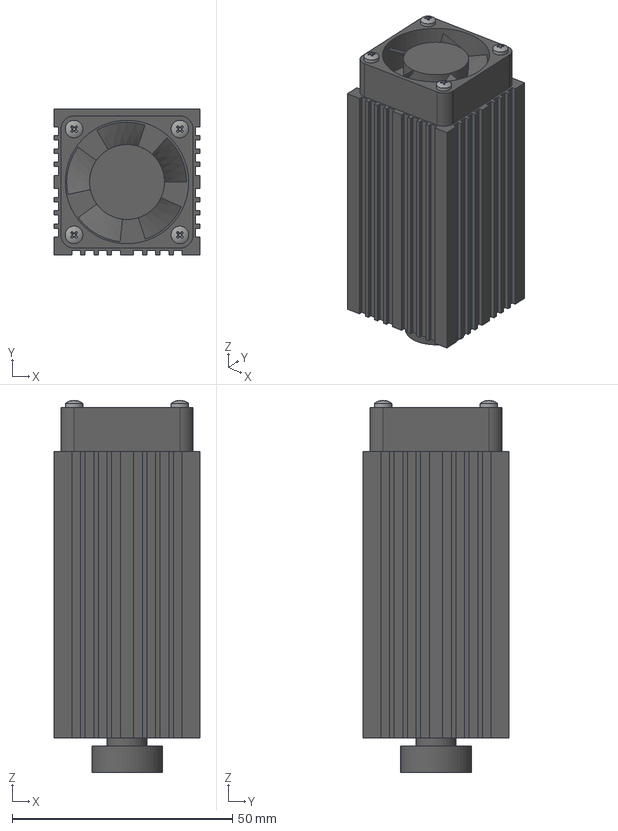
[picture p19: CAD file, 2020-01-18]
CAD/Electronics/Laser Module 5500mW.FCStd
33.0 x 33.0 x 84.4 mm
M2x10-Screw
M2x10-Screw001
M2x10-Screw002
M2x10-Screw003

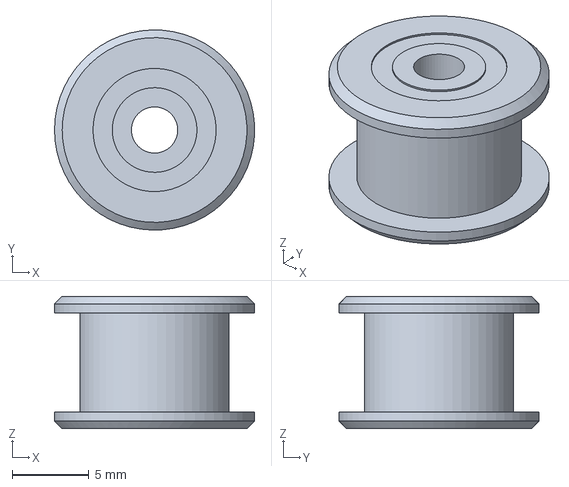
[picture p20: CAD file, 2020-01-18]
CAD/Mechanical/Pulley.fcstd
13.0 x 13.0 x 8.60 mm

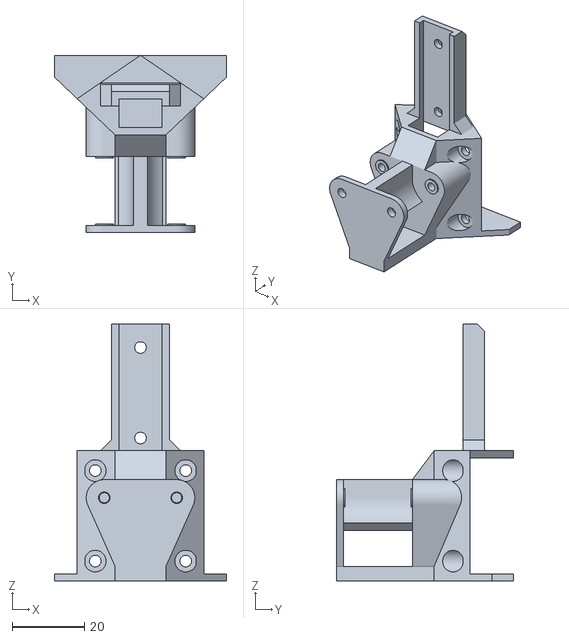
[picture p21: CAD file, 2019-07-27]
STLs/Rail Base.stl
47.6 x 49.0 x 71.0

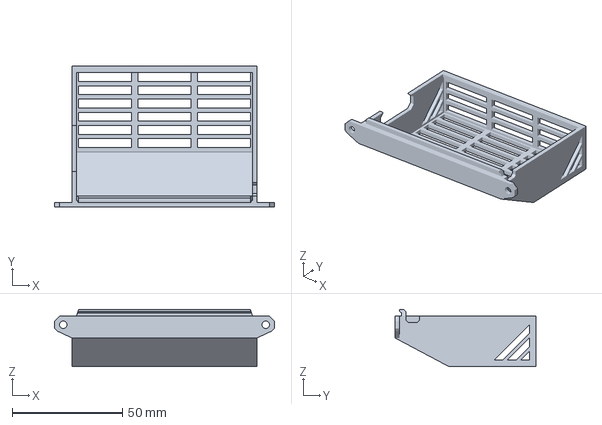
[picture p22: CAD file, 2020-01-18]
AMFs/Controller Case Top.amf
100.0 x 64.0 x 26.0 mm

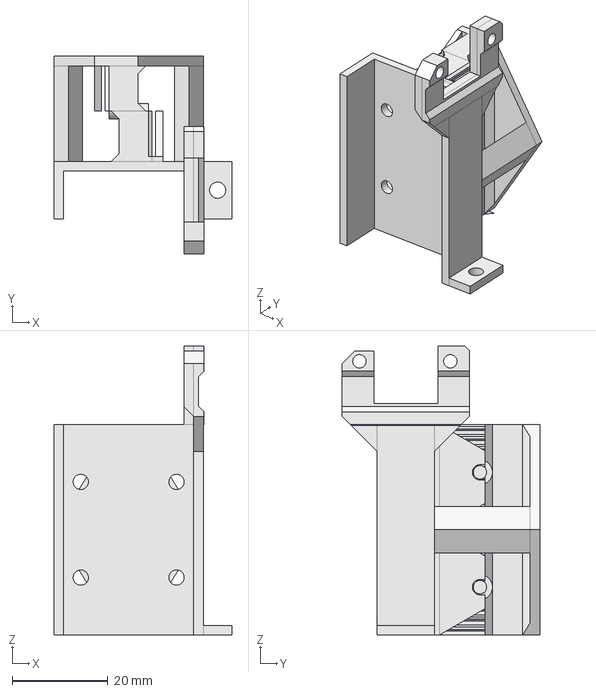
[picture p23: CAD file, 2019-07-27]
CAD/3D Printed/Rail Carrier.FCStd
37.2 x 41.3 x 60.4 mm

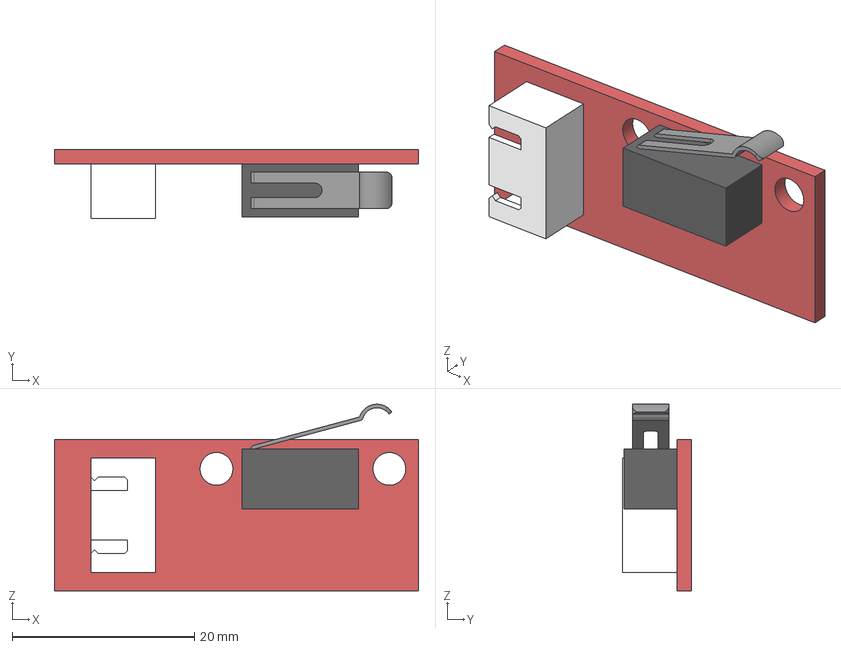
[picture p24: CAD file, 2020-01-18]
CAD/Electronics/Endstop.FCStd
40.0 x 7.60 x 20.5 mm
PCB
Connector
Switch
Lever

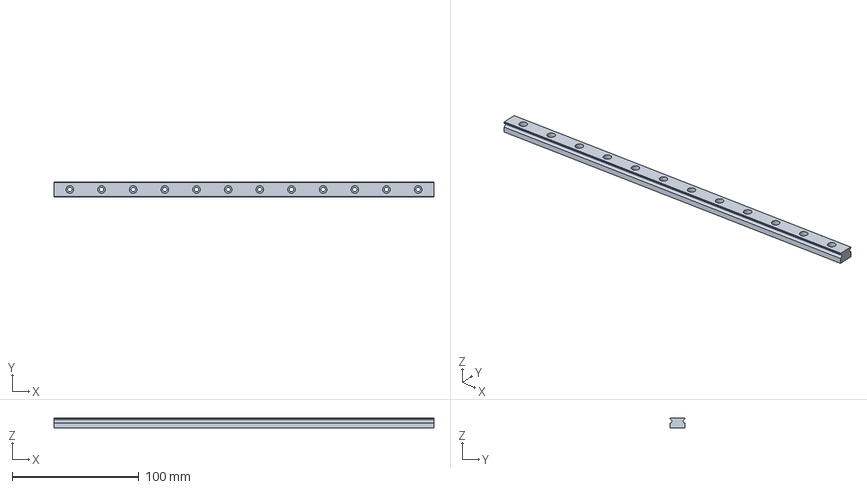
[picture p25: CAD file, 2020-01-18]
CAD/Mechanical/Rail MGN12 300mm.fcstd
300.0 x 12.0 x 8.00 mm

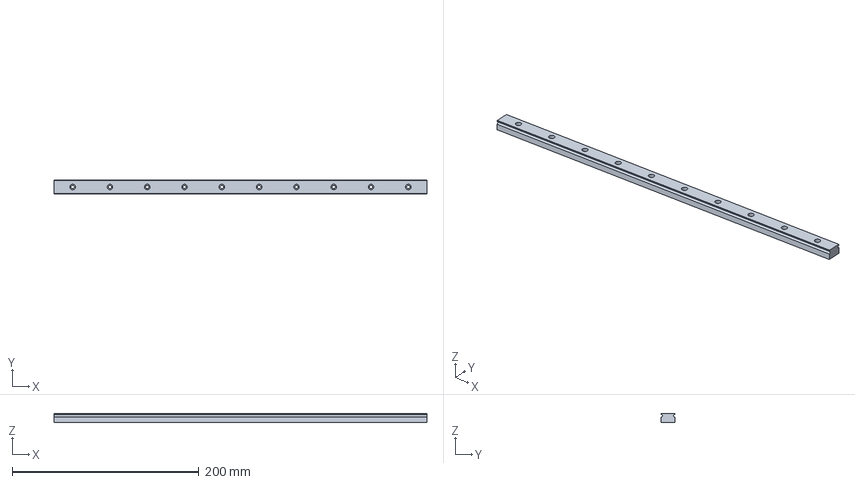
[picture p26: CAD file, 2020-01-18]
CAD/Mechanical/Rail MGN15 400mm.fcstd
400.0 x 15.0 x 10.0 mm

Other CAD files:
CAD/3D Printed/Rail Tip.FCStd
AMFs/Motor Mount Right.amf
CAD/3D Printed/Pulley Cage Left.FCStd
AMFs/Base Left.amf
AMFs/Base Middle.amf
AMFs/Base Right.amf
AMFs/Bottom Stand.amf
AMFs/Controller Case Bottom.amf
AMFs/Endstop Mount.amf
AMFs/Laser Mount.amf
AMFs/Laser PCB Box Lid.amf
AMFs/Laser PCB Box.amf
AMFs/Pulley Cage Left.amf
AMFs/Pulley Cage Right.amf
AMFs/Rail Base.amf
AMFs/Rail Carrier.amf
AMFs/Spacer.amf
AMFs/Tall Spacer.amf
CAD/3D Printed/Base Left.FCStd
CAD/3D Printed/Base Middle.FCStd
CAD/3D Printed/Base Right.FCStd
CAD/3D Printed/Bottom Stand.FCStd
CAD/3D Printed/Controller Case Bottom.FCStd
CAD/3D Printed/Controller Case Top.FCStd
CAD/3D Printed/Endstop Mount.FCStd
CAD/3D Printed/Laser Mount.FCStd
CAD/3D Printed/Laser PCB Box Lid.FCStd
CAD/3D Printed/Laser PCB Box.FCStd
CAD/3D Printed/Motor Mount Left.FCStd
CAD/3D Printed/Motor Mount Right.FCStd
CAD/3D Printed/Rail Base.FCStd
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

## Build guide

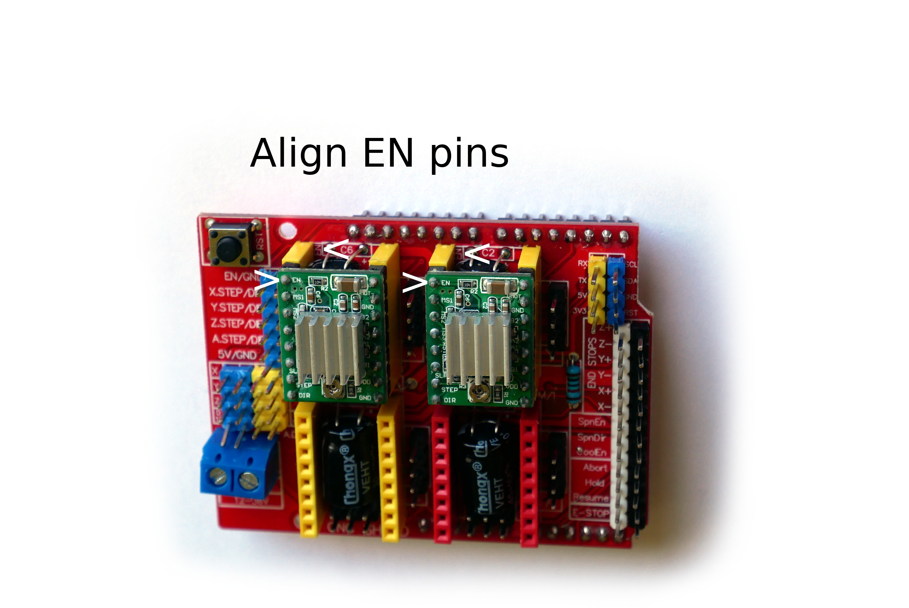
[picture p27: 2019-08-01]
images/Controller Assembly 3 Steppers.JPG

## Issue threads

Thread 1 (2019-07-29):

Would you be willing to announce and discuss your process of creating this on the FreeCAD forums?

luzpaz, 2019-07-29:
Specifically the FreeCAD [Users Showcases subforum](https://forum.freecadweb.org/viewforum.php?f=24) ?

FiCacador, 2019-07-30:
Sure, but I won't be able to do it during the next couple of weeks.
Once I add a few more things to this project and have the time for it, I will register and create a topic there.

luzpaz, 2019-09-26:
Soft bump.

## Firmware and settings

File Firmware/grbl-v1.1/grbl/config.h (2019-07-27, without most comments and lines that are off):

#define config_h
#include "grbl.h" // For Arduino IDE compatibility.
#define DEFAULTS_TLASER // Tlaser default settings
#define CPU_MAP_ATMEGA328P // Arduino Uno CPU
#define BAUD_RATE 115200
#define CMD_RESET 0x18 // ctrl-x.
#define CMD_STATUS_REPORT '?'
#define CMD_CYCLE_START '~'
#define CMD_FEED_HOLD '!'
#define CMD_SAFETY_DOOR 0x84
#define CMD_JOG_CANCEL  0x85
#define CMD_DEBUG_REPORT 0x86 // Only when DEBUG enabled, sends debug report in '{}' braces.
#define CMD_FEED_OVR_RESET 0x90         // Restores feed override value to 100%.
#define CMD_FEED_OVR_COARSE_PLUS 0x91
#define CMD_FEED_OVR_COARSE_MINUS 0x92
#define CMD_FEED_OVR_FINE_PLUS  0x93
#define CMD_FEED_OVR_FINE_MINUS  0x94
#define CMD_RAPID_OVR_RESET 0x95        // Restores rapid override value to 100%.
#define CMD_RAPID_OVR_MEDIUM 0x96
#define CMD_RAPID_OVR_LOW 0x97
#define CMD_SPINDLE_OVR_RESET 0x99      // Restores spindle override value to 100%.
#define CMD_SPINDLE_OVR_COARSE_PLUS 0x9A
#define CMD_SPINDLE_OVR_COARSE_MINUS 0x9B
#define CMD_SPINDLE_OVR_FINE_PLUS 0x9C
#define CMD_SPINDLE_OVR_FINE_MINUS 0x9D
#define CMD_SPINDLE_OVR_STOP 0x9E
#define CMD_COOLANT_FLOOD_OVR_TOGGLE 0xA0
#define CMD_COOLANT_MIST_OVR_TOGGLE 0xA1
#define HOMING_INIT_LOCK // Comment to disable
#define HOMING_CYCLE_0 (1<<X_AXIS)                // COREXY COMPATIBLE: First home X.
#define HOMING_CYCLE_1 (1<<Y_AXIS)                // COREXY COMPATIBLE: Then home Y
#define N_HOMING_LOCATE_CYCLE 1 // Integer (1-128)
#define HOMING_FORCE_SET_ORIGIN // Uncomment to enable.
#define N_STARTUP_LINE 2 // Integer (1-2)
#define N_DECIMAL_COORDVALUE_INCH 4 // Coordinate or position value in inches
#define N_DECIMAL_COORDVALUE_MM   3 // Coordinate or position value in mm
#define N_DECIMAL_RATEVALUE_INCH  1 // Rate or velocity value in in/min
#define N_DECIMAL_RATEVALUE_MM    0 // Rate or velocity value in mm/min
#define N_DECIMAL_SETTINGVALUE    3 // Decimals for floating point setting values
#define N_DECIMAL_RPMVALUE        0 // RPM value in rotations per min.
#define SAFETY_DOOR_SPINDLE_DELAY 4.0 // Float (seconds)
#define SAFETY_DOOR_COOLANT_DELAY 1.0 // Float (seconds)
#define COREXY // Default disabled. Uncomment to enable.
#define DEFAULT_FEED_OVERRIDE           100 // 100%. Don't change this value.
#define MAX_FEED_RATE_OVERRIDE          200 // Percent of programmed feed rate (100-255). Usually 120% or 200%
#define MIN_FEED_RATE_OVERRIDE           10 // Percent of programmed feed rate (1-100). Usually 50% or 1%
#define FEED_OVERRIDE_COARSE_INCREMENT   10 // (1-99). Usually 10%.
#define FEED_OVERRIDE_FINE_INCREMENT      1 // (1-99). Usually 1%.
#define DEFAULT_RAPID_OVERRIDE  100 // 100%. Don't change this value.
#define RAPID_OVERRIDE_MEDIUM    50 // Percent of rapid (1-99). Usually 50%.
#define RAPID_OVERRIDE_LOW       25 // Percent of rapid (1-99). Usually 25%.
#define DEFAULT_SPINDLE_SPEED_OVERRIDE    100 // 100%. Don't change this value.
#define MAX_SPINDLE_SPEED_OVERRIDE        200 // Percent of programmed spindle speed (100-255). Usually 200%.
#define MIN_SPINDLE_SPEED_OVERRIDE         10 // Percent of programmed spindle speed (1-100). Usually 10%.
#define SPINDLE_OVERRIDE_COARSE_INCREMENT  10 // (1-99). Usually 10%.
#define SPINDLE_OVERRIDE_FINE_INCREMENT     1 // (1-99). Usually 1%.
#define RESTORE_OVERRIDES_AFTER_PROGRAM_END // Default enabled. Comment to disable.
#define REPORT_FIELD_BUFFER_STATE // Default enabled. Comment to disable.
#define REPORT_FIELD_PIN_STATE // Default enabled. Comment to disable.
#define REPORT_FIELD_CURRENT_FEED_SPEED // Default enabled. Comment to disable.
#define REPORT_FIELD_WORK_COORD_OFFSET // Default enabled. Comment to disable.
#define REPORT_FIELD_OVERRIDES // Default enabled. Comment to disable.
#define REPORT_FIELD_LINE_NUMBERS // Default enabled. Comment to disable.
#define REPORT_OVR_REFRESH_BUSY_COUNT 20  // (1-255)
#define REPORT_OVR_REFRESH_IDLE_COUNT 10  // (1-255) Must be less than or equal to the busy count
#define REPORT_WCO_REFRESH_BUSY_COUNT 30  // (2-255)
#define REPORT_WCO_REFRESH_IDLE_COUNT 10  // (2-255) Must be less than or equal to the busy count
#define ACCELERATION_TICKS_PER_SECOND 100
#define ADAPTIVE_MULTI_AXIS_STEP_SMOOTHING  // Default enabled. Comment to disable.
#define TOOL_LENGTH_OFFSET_AXIS Z_AXIS // Default z-axis. Valid values are X_AXIS, Y_AXIS, or Z_AXIS.
#define VARIABLE_SPINDLE // Default enabled. Comment to disable.
#define MINIMUM_JUNCTION_SPEED 0.0 // (mm/min)
#define MINIMUM_FEED_RATE 1.0 // (mm/min)
#define N_ARC_CORRECTION 12 // Integer (1-255)
#define ARC_ANGULAR_TRAVEL_EPSILON 5E-7 // Float (radians)
#define DWELL_TIME_STEP 50 // Integer (1-255) (milliseconds)
#define ENABLE_RESTORE_EEPROM_WIPE_ALL         // '$RST=*' Default enabled. Comment to disable.
#define ENABLE_RESTORE_EEPROM_DEFAULT_SETTINGS // '$RST=$' Default enabled. Comment to disable.
#define ENABLE_RESTORE_EEPROM_CLEAR_PARAMETERS // '$RST=#' Default enabled. Comment to disable.
#define ENABLE_BUILD_INFO_WRITE_COMMAND // '$I=' Default enabled. Comment to disable.
#define FORCE_BUFFER_SYNC_DURING_EEPROM_WRITE // Default enabled. Comment to disable.
#define FORCE_BUFFER_SYNC_DURING_WCO_CHANGE // Default enabled. Comment to disable.
#define PARKING_AXIS Z_AXIS // Define which axis that performs the parking motion
#define PARKING_TARGET -5.0 // Parking axis target. In mm, as machine coordinate [-max_travel,0].
#define PARKING_RATE 500.0 // Parking fast rate after pull-out in mm/min.
#define PARKING_PULLOUT_RATE 100.0 // Pull-out/plunge slow feed rate in mm/min.
#define PARKING_PULLOUT_INCREMENT 5.0 // Spindle pull-out and plunge distance in mm. Incremental distance.
#define DISABLE_LASER_DURING_HOLD // Default enabled. Comment to disable.
#define N_PIECES 4  // Integer (1-4). Number of piecewise lines used in script solution.
#define RPM_MAX  11686.4  // Max RPM of model. $30 > RPM_MAX will be limited to RPM_MAX.
#define RPM_MIN  202.5    // Min RPM of model. $31 < RPM_MIN will be limited to RPM_MIN.
#define RPM_POINT12  6145.4  // Used N_PIECES >=2. Junction point between lines 1 and 2.
#define RPM_POINT23  9627.8  // Used N_PIECES >=3. Junction point between lines 2 and 3.
#define RPM_POINT34  10813.9 // Used N_PIECES = 4. Junction point between lines 3 and 4.
#define RPM_LINE_A1  3.197101e-03  // Used N_PIECES >=1. A and B constants of line 1.
#define RPM_LINE_B1  -3.526076e-1
#define RPM_LINE_A2  1.722950e-2   // Used N_PIECES >=2. A and B constants of line 2.
#define RPM_LINE_B2  8.588176e+01
#define RPM_LINE_A3  5.901518e-02  // Used N_PIECES >=3. A and B constants of line 3.
#define RPM_LINE_B3  4.881851e+02
#define RPM_LINE_A4  1.203413e-01  // Used N_PIECES = 4. A and B constants of line 4.
#define RPM_LINE_B4  1.151360e+03
  #define DEFAULT_X_STEPS_PER_MM 100.0
  #define DEFAULT_Y_STEPS_PER_MM 100.0
  #define DEFAULT_Z_STEPS_PER_MM 250.0
  #define DEFAULT_X_MAX_RATE 12000.0 // mm/min
  #define DEFAULT_Y_MAX_RATE 12000.0 // mm/min
  #define DEFAULT_Z_MAX_RATE 500.0 // mm/min
  #define DEFAULT_X_ACCELERATION (2000.0*60*60) // 10*60*60 mm/min^2 = 10 mm/sec^2
  #define DEFAULT_Y_ACCELERATION (2000.0*60*60) // 10*60*60 mm/min^2 = 10 mm/sec^2
  #define DEFAULT_Z_ACCELERATION (10.0*60*60) // 10*60*60 mm/min^2 = 10 mm/sec^2
  #define DEFAULT_X_MAX_TRAVEL 315.0 // mm NOTE: Must be a positive value.
  #define DEFAULT_Y_MAX_TRAVEL 205.0 // mm NOTE: Must be a positive value.
  #define DEFAULT_Z_MAX_TRAVEL  10.0 // mm NOTE: Must be a positive value.
  #define DEFAULT_SPINDLE_RPM_MAX 1000.0 // rpm
  #define DEFAULT_SPINDLE_RPM_MIN 0.0 // rpm
  #define DEFAULT_STEP_PULSE_MICROSECONDS 3
  #define DEFAULT_STEPPING_INVERT_MASK 0
  #define DEFAULT_DIRECTION_INVERT_MASK 0
  #define DEFAULT_STEPPER_IDLE_LOCK_TIME 25 // msec (0-254, 255 keeps steppers enabled)
  #define DEFAULT_STATUS_REPORT_MASK 1 // MPos enabled
  #define DEFAULT_JUNCTION_DEVIATION 0.03 // mm
  #define DEFAULT_ARC_TOLERANCE 0.002 // mm
  #define DEFAULT_REPORT_INCHES 0 // false
  #define DEFAULT_INVERT_ST_ENABLE 0 // false
  #define DEFAULT_INVERT_LIMIT_PINS 0 // false
  #define DEFAULT_SOFT_LIMIT_ENABLE 1 // true
  #define DEFAULT_HARD_LIMIT_ENABLE 0  // false
  #define DEFAULT_INVERT_PROBE_PIN 0 // false
  #define DEFAULT_LASER_MODE 1 // true
  #define DEFAULT_HOMING_ENABLE 1  // true
  #define DEFAULT_HOMING_DIR_MASK 3 // move negative dir XY
  #define DEFAULT_HOMING_FEED_RATE 1200.0 // mm/min
  #define DEFAULT_HOMING_SEEK_RATE 2400.0 // mm/min
  #define DEFAULT_HOMING_DEBOUNCE_DELAY 250 // msec (0-65k)
  #define DEFAULT_HOMING_PULLOFF 2.0 // mm

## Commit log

2019-07-29 Add Bill of Materials
    [BOM.ods]
2019-07-30 Replace wrong STL file
    [Motor Mount Right.stl]
2019-07-31 Add video and Grbl links to README
2019-08-01 Add Exploded Assembly
2019-08-01 Add controller assembly images
2019-08-01 Add exploded assembly image
2020-01-18 Add AMF files
    Add AMF type files for 3D printing.
    AMF files are smaller in size and contain more information compared with traditional STL files.
    If you use Cura, at least version 4.4 is required for AMF import to work correctly.
    [Base Left.amf, Base Middle.amf, Base Right.amf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]
2020-01-18 Add CAD images with updated appearance
2020-01-18 Update appearance
    [Endstop.FCStd, Laser Module 5500mW.FCStd, Stepper motor Nema 17 42BYGH 38mm.fcstd]
2020-03-22 Add Exploded Assembly Video link to README
2020-03-26 Update BOM and add xlsx format
    [BOM.ods, BOM.xlsx]

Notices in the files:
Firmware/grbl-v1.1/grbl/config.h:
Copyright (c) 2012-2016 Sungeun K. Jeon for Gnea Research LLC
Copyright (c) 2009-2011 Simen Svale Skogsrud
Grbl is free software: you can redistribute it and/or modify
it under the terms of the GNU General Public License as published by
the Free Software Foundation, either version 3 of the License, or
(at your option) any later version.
